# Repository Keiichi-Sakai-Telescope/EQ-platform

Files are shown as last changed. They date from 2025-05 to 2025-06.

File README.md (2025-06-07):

## これは何か？

40cmドブソニアンなどに使っている赤道台(Equatorial Platform)の設計や実験の結果など雑多なものを置いています。タミヤの6速HEというギヤボックスを活用して低消費電力な追尾を目指していました。RE-260互換モーターをそのまま使用し、センサなしで恒星時追尾します。
もともと55cmドブソニアンのポンセットマウントを作ってたので、Poncetという単語が散見されますが、それすらGee式で、最終的な実装のかたちは独自形式です。もし読めそうなファイルがあれば眺めていただければと思います。

このプロジェクトはSubversionで管理していましたが、データシートなど大きなバイナリを含んでいたため、gitに変換すると非常に大きくなったために、主要なファイルのみgithubに上げることにしました。
そういう経緯のためにgit cloneしたところで何かできるものではなく、過去にこんなの作って実験してましたという記録を残すことが目的です。プロジェクトの残骸ですね。。。

## 開発環境

* MPLAB X<br/>新しくても古くても動かないと思います。アセンブラとリンカーがよく変わるので、動くバージョンを探す必要があります。
* XCircuit<br/>Linux環境で使っていた回路図CADです。
* Pcb<br/>Linux環境で使っていたプリント基板CADです。
* QCad もしくは LibreCAD<br/>2D CADです。ファイルはDXF形式ですが、LibreCADでもQCadでも見栄えがよく変わります。標準規格がないんですね。
* GNU bc<br/>任意精度の計算コマンドです。表引き用の数値を計算するのに使ってました。

## MPLab Xのプロジェクトたち

複数試作しましたが、世の中に出回っている基板はPIC16F1825を使った新旧2種類の基板のみです。外見上の区別は3.5mmミニジャックがある(新)かない(古)か、内部ではMOSFETの駆動用にインバータICが入ってる(新)か入ってない(古)かです。

* FB-UB-16F18345.X<br/>PIC16F18345による試作です。これを実装した架台は無いです。
* FB-UB-16F18857.X<br/>PIC16F18857による試作です。これを実装した架台は無いです。
* FB-UB-18F25Q10.X<br/>PIC18F25Q10による試作です。これを実装した架台は無いです。
* FB-USB.X<br/>検討のみ。試作してない。
* FB-minimal.X<br/>検討のみ。試作してない。
* Flasher.X<br/>ストロボスコープを持ち歩くのは大げさなので、PIC16F1825基板を流用してLEDによるストロボスコープもどきを作ってました。
* HB-B-16F1825.X<br/>PIC16F1825による実装です。5.5Vまで動作することを目指しています。3.5mmステレオジャックを実装している新しい基板ではこのソフトウェアを書き込む必要があります。電源電圧の変化には安定ですが、ADCのVrefを2.048V設定とすることによる動作下限電圧があります。
* HB-B-16LF1825.X<br/>PIC16F1825による実装です。MCUの動作下限電圧まで動作することを目指しています。3.5mmステレオジャックを実装している新しい基板ではこのソフトウェアを書き込む必要があります。LF版MCUによる実装を目指していましたが、LF版を使う強い理由がなくてLF版で実装してません。ADCのVrefが電源電圧なので、5V近くなると1LSBの電圧が大きくなって制御が不安定になるかもしれません。
* HB-CC.X<br/>検討のみ。試作してない。
* HB-UB-16F1825.X<br/>PIC16F1825による実装です。5.5Vまで動作することを目指しています。3.5mmステレオジャックを実装していない古い基板ではこのソフトウェアを書き込む必要があります。電源電圧の変化には安定ですが、ADCのVrefを2.048V設定とすることによる動作下限電圧があります。
* HB-UB-16LF1825.X<br/>PIC16F1825による実装です。MCUの動作下限電圧まで動作することを目指しています。3.5mmステレオジャックを実装していない古い基板ではこのソフトウェアを書き込む必要があります。LF版MCUによる実装を目指していましたが、LF版を使う強い理由がなくてLF版で実装してません。ADCのVrefが電源電圧なので、5V近くなると1LSBの電圧が大きくなって制御が不安定になるかもしれません。
* HB-VC.X<br/>検討のみ。試作してない。

乾電池やニッケル水素充電池を3本使用し、新しい基板ならHB-B-16F1825.Xからのソフトウェアを書き込むとよいはずです。
SP赤道儀など軽負荷の場合は電池2本でも動きますが、2本の場合はHB-B-16LF1825.Xを使う必要があります。

## 外部信号

* 巻き戻しSW<br/>
追尾開始位置を知らせるスイッチを接続します。必須です。
* 動作限界SW<br/>
単方向噛合ナット(改造したウルトラナッターなど)を使ってない場合、動作限界を超えたら止めるように指示するスイッチを接続します。単方向噛合ナットを使っている場合は空回りするだけなので不要です。
* 停止SW<br/>
半自動追尾のときの停止スイッチを接続します。新しい基板では3.5mmミニジャックを接続端子として実装しています。
* 2倍速SW<br/>
半自動追尾のときの2倍速スイッチを接続します。新しい基板では3.5mmミニジャックを接続端子として実装しています。

## ギヤボックスやモーターなど

タミヤの6速HEとそれに付属するRE-260モーターに合わせてありますが、モーター定数定義を替えることにより他のマブチ互換の模型用モーターでも動きます。
なお、モーターの回転数が定格の1/10くらいのところで一定速度の制御をかけるように設計されており、motor.incにモーター定数が定義されています。
そして、たとえば6-speed-4th-40min-16in.sが現在使用中の40cmドブソニアンの追尾架台に組み込んでいる速度表です。この速度票を巻き戻したときに頭から読み、最後に達したら止まります。
また、有限の速度表を使わず、表を無限に循環して使用する設定もでき、SP赤道儀向けなどではそうしています。いずれにせよ、motor.incに記述があるので読んでください。

本実装ではタミヤの6速HE推しですが、これは安いし入手性がいいし6速から選べるし1300分の1まで減速できるし平歯車だけで構成されてていずれも高効率なため、SP赤道儀といった軽負荷用途にもアンバランスな追尾架台といった重負荷用途にも最適であると考えています。
実際に、SP赤道儀のような軽負荷では消費電流20mA前後、40㎝ドブソニアンのような重負荷用途では消費電流100mA前後となります。エネループ単三でそれぞれ100時間と20時間相当です。

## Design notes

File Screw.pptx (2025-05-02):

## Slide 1

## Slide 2

トルク
ピッチ
有効径
リード角
摩擦係数
摩擦角
頂角÷２

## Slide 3

トルク[kgf-cm]
ピッチ = 1.75mm
有効径 = 10.863mm
リード角 = 2.938° = 0.0513 rad
摩擦係数 = 0.3
摩擦角 = 19.848° = 0.3464 rad
頂角÷２ = 30° = π/6 rad

M12P1.75, μ=0.3 で持ち上げる場合

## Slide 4

トルク[kgf-cm]
ピッチ = 1.75mm
有効径 = 10.863mm
リード角 = 2.938° = 0.0513 rad
摩擦係数 = 0.3
摩擦角 = 19.848° = 0.3464 rad
頂角÷２ = 30° = π/6 rad

M12P1.75, μ=0.3 で繰り下げる場合

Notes: p=1.75
d=10.863
m=0.3
20/d/t(a(m/c(3.14159/6))-a(p/d/3.14159))

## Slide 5

トルク[kgf-cm]
ピッチ = 25.4/16 mm = 1.5875mm
有効径 = 8.509mm
リード角
摩擦係数 = 0.3
摩擦角
頂角÷２ = 27.5° = 55π/360 rad

W3/8 16T/in, μ=0.3 で持ち上げる場合
繰り下げる場合は8.60T

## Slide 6

トルク[kgf-cm]
ピッチ = 49/17 mm = 2.88mm
有効径 = 4mm
リード角=0.225[rad]
摩擦係数 = 0.3
摩擦角
頂角÷２ = 27.5° = 55π/360 rad

細軸コース, μ=0.3 で持ち上げる場合
繰り下げる場合は44T

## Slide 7

正三角形

z

y

60°

x

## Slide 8

南天赤道儀？

z

y

φ

x

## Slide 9

z

y

90°

x

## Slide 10

y

天板

90-緯度

0

x

x軸が蝶番の軸

底板

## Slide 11

t, δは分の単位とすると
motor_speedはrpmの単位となる。
そのとき、ω=2π/1436.0681755 である。
同様にt, δが秒の単位では、
motor_speedはrpsの単位で、
ω=2π/86164.09053 である。

y

＋　　　　　　ー

y

0

90-緯度

x

z

x軸が蝶番の軸

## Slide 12

固定点と可動点を任意に置く場合

可動点

図のような位置に固定点を置くと、
固定点の角度変化が少なくなる。
ナットを固定点側に置くのも良いかも。
固定と可動は図を書く都合なので、
入れ替えて考えることは可能。

固定点

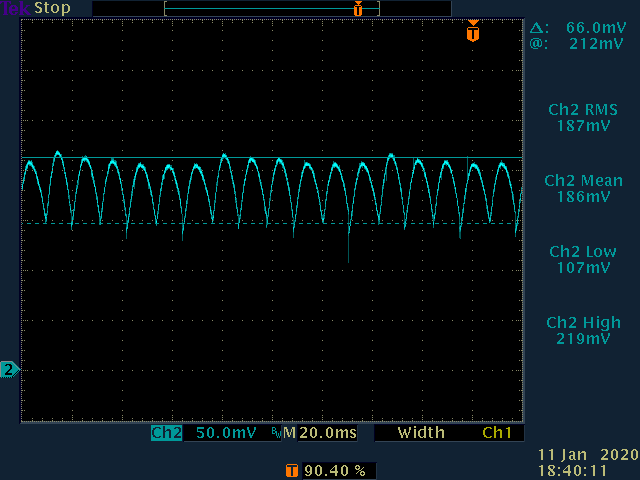
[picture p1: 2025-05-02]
900rpm_RE-260_new_mabuchi.TIF

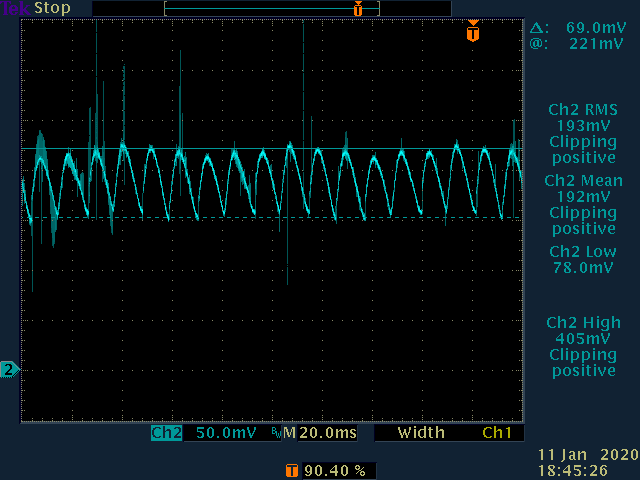
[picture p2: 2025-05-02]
900rpm_RE-260_asahi.TIF

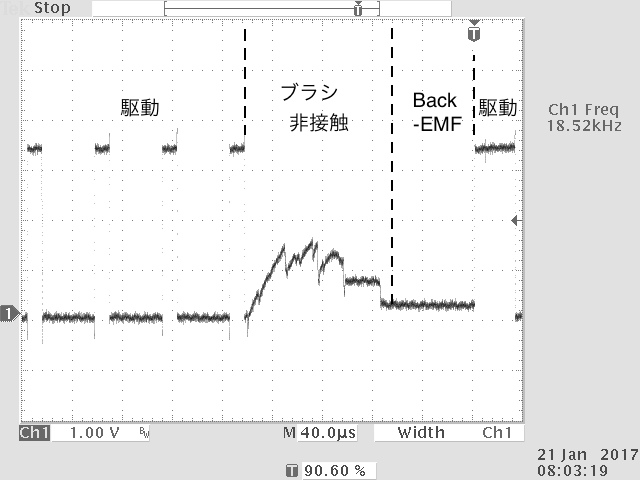
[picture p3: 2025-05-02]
inv-TEK00004.png

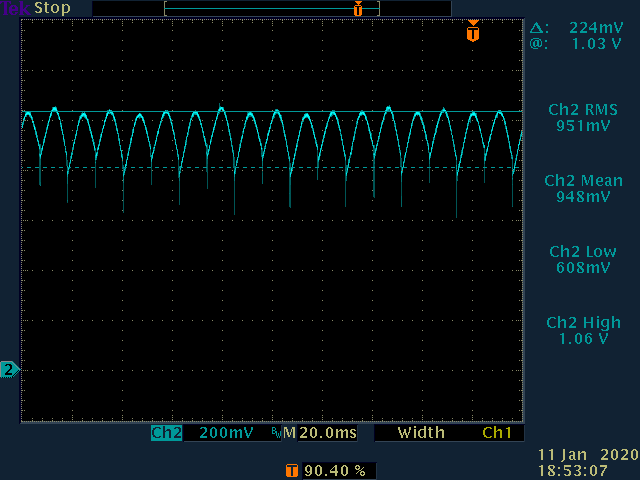
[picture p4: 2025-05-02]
900rpm_RF-500_mabuchi.TIF

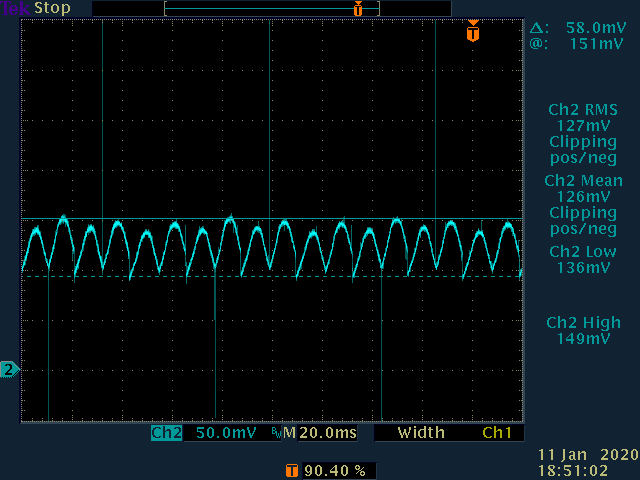
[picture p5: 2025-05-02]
900rpm_FA-130_new_mabuchi.TIF

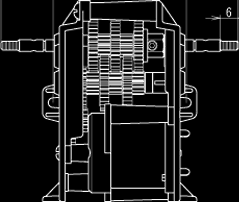
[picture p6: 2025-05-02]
72005-top.png

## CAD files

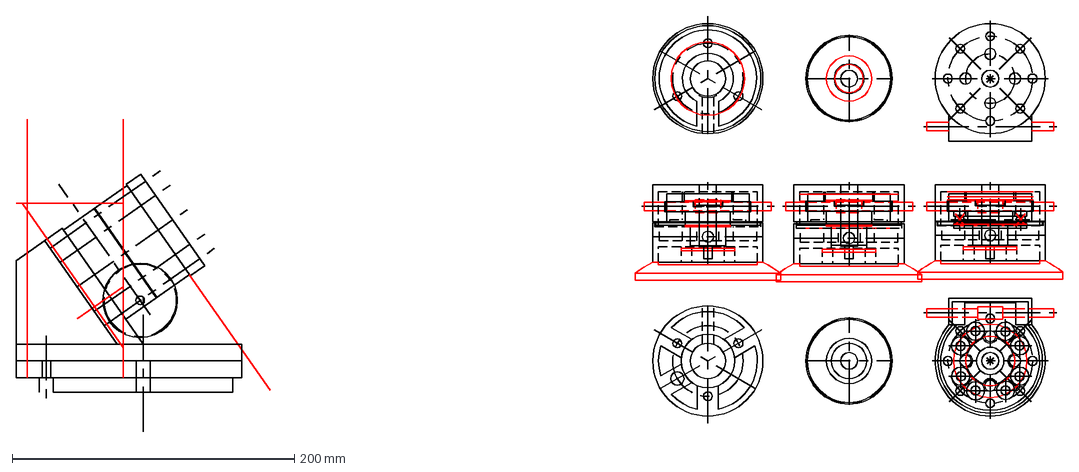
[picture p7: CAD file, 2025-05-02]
Porta.dxf
741.5 x 294.0 mm

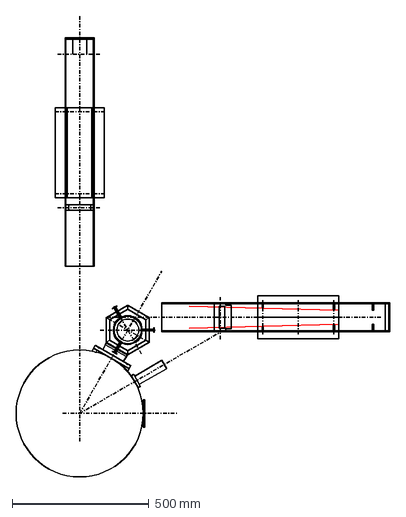
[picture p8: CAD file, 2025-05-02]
8cm-Mount.dxf
1365.0 x 1683.3 mm

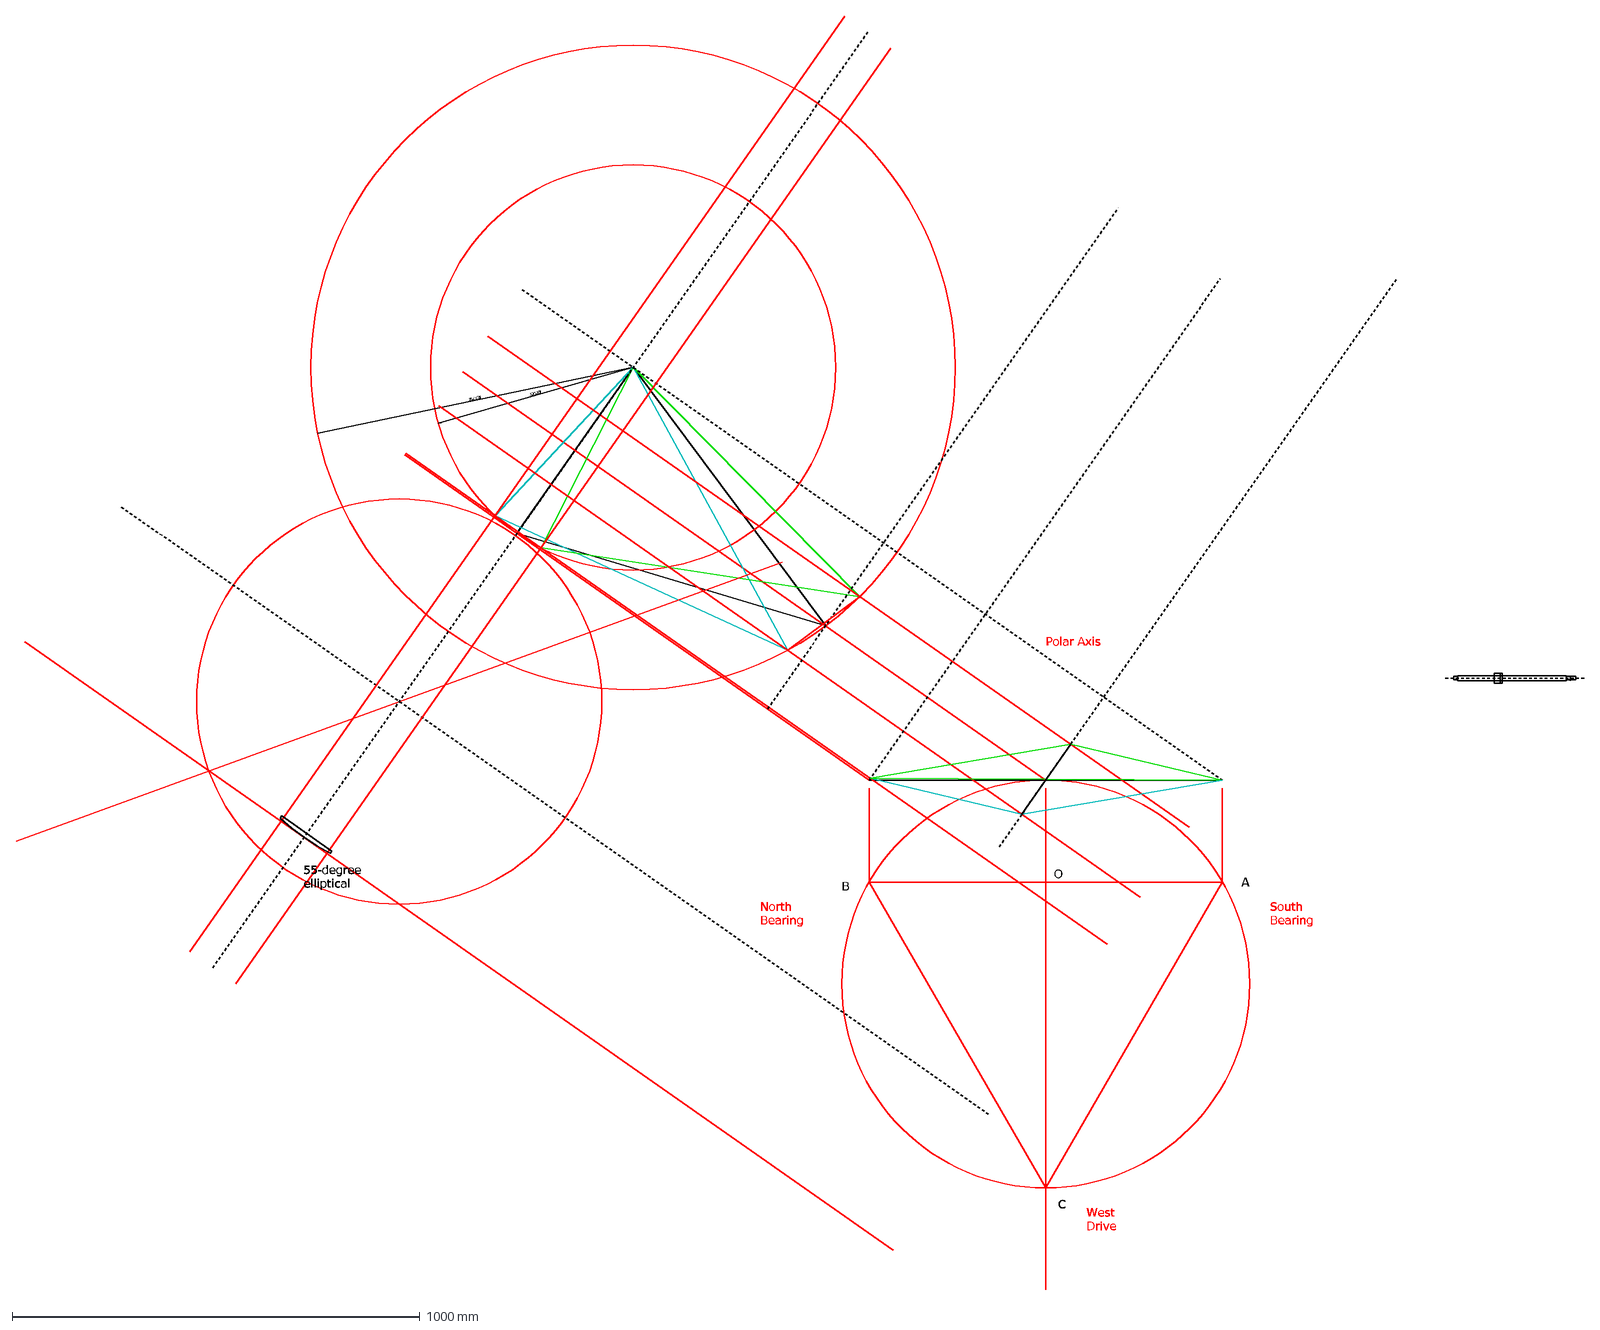
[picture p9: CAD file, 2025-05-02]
Unbalanced-EQ-8cm-Type1.dxf
496,73
790,05
A
B
C
O
South Bearing
North Bearing
West Drive
Polar Axis
55-degree elliptical

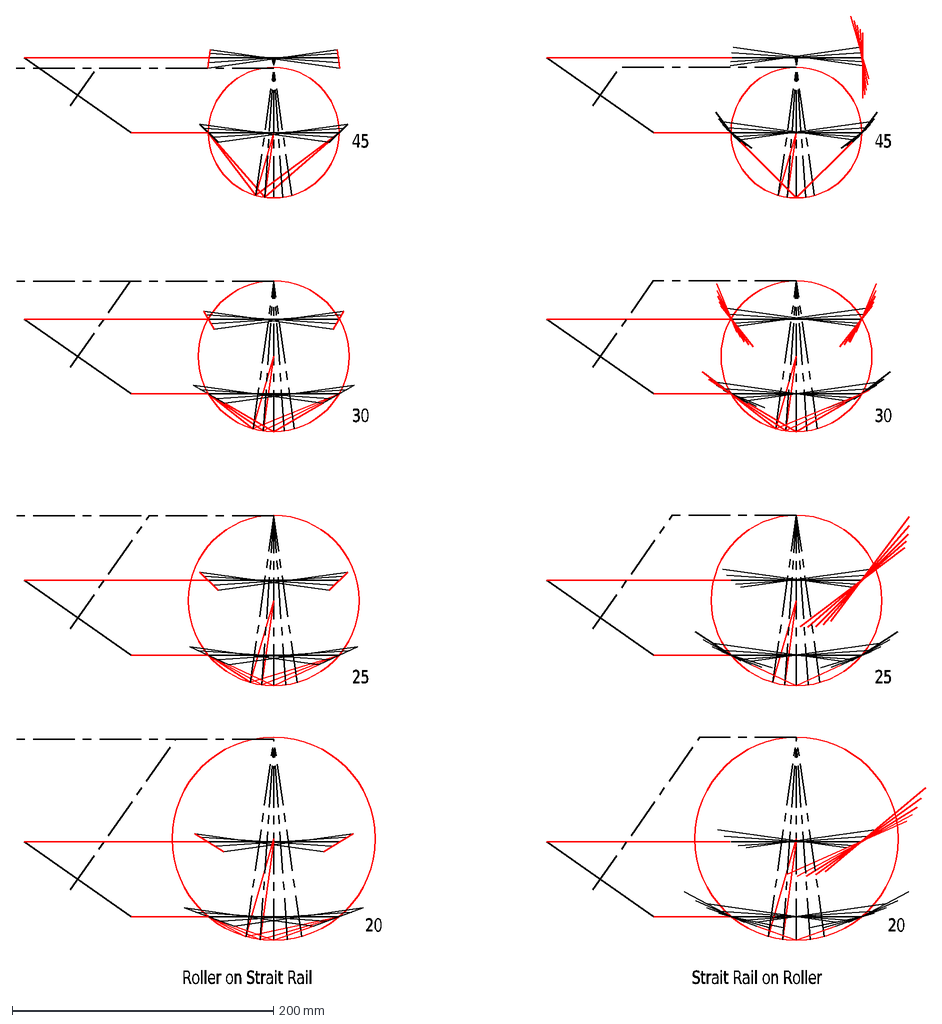
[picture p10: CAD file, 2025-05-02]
circumferential.dxf
Roller\~on\~Strait\~Rail
20
25
30
45
Strait\~Rail\~on\~Roller

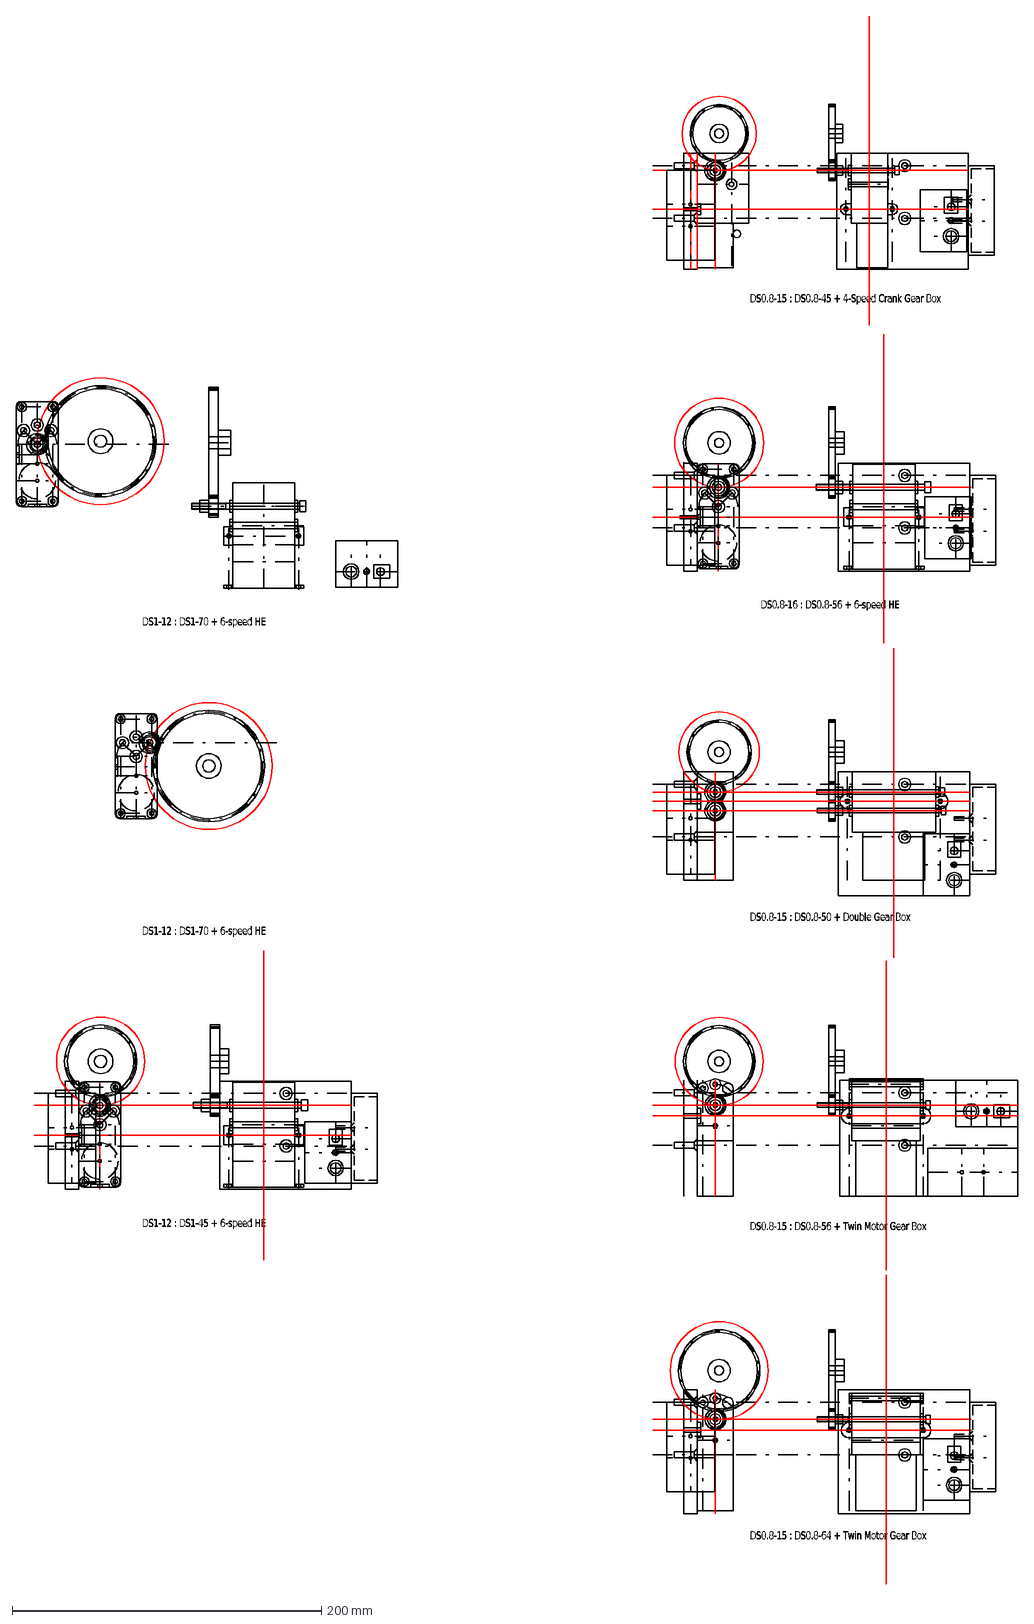
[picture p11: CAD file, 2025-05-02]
6-Speed_HE.dxf
DS1-12\~:\~DS1-70\~+\~6-speed\~HE
DS1-12\~:\~DS1-45\~+\~6-speed\~HE
DS0.8-16\~:\~DS0.8-56\~+\~6-speed\~HE
DS0.8-15\~:\~DS0.8-50\~+\~Double\~Gear\~Box
DS0.8-15\~:\~DS0.8-45\~+\~4-Speed\~Crank\~Gear\~Box
DS0.8-15\~:\~DS0.8-56\~+\~Twin\~Motor\~Gear\~Box
DS0.8-15\~:\~DS0.8-64\~+\~Twin\~Motor\~Gear\~Box

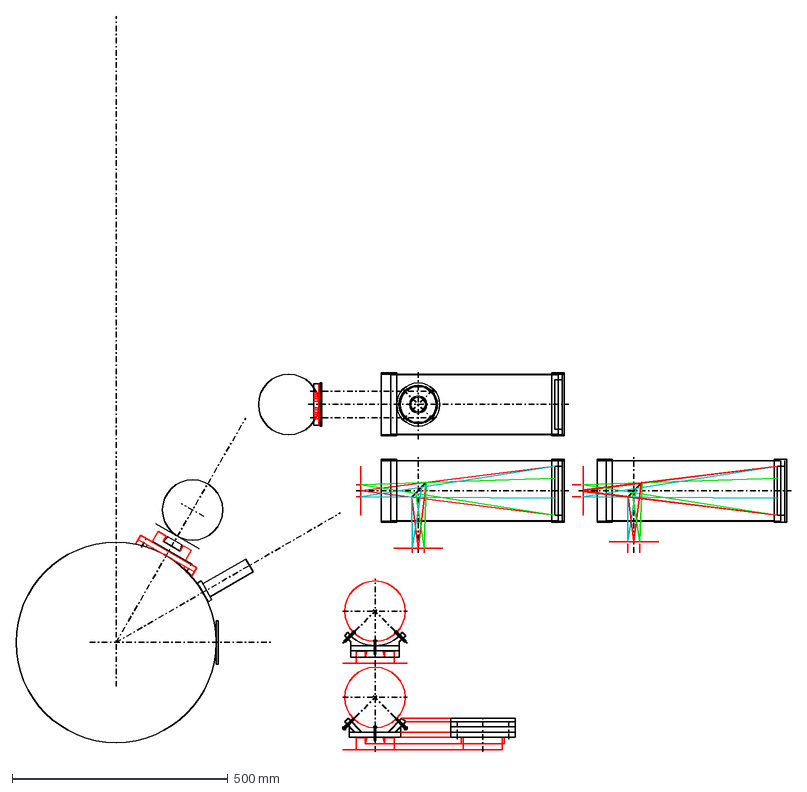
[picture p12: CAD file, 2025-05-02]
SE-AT100n-Mount.dxf
1796.0 x 1705.0 mm

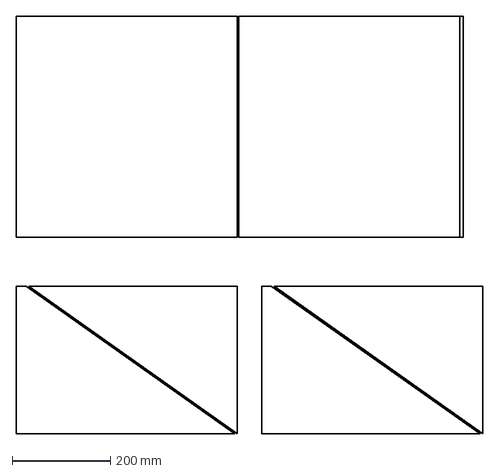
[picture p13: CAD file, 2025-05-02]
cutting-plan.dxf
950.0 x 850.0 mm

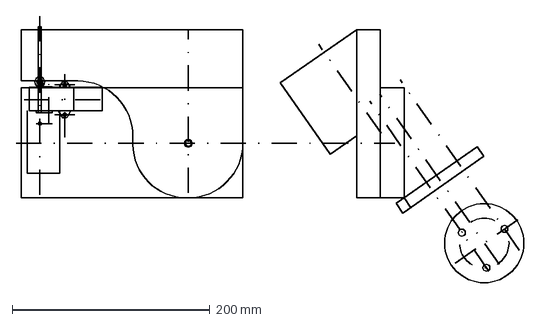
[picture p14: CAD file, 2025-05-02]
Kolkit.dxf
512.9 x 269.1 mm

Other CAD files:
Poncet450.dxf
16in-Tube.dxf
Unbalanced-EQ-8cm-Type2.dxf
SuperPolaris.dxf
GearBox.dxf
16in-Mount.dxf
Poncet480-mirrored-hinge.dxf
Gee-8cm.dxf
Poncet480.dxf
Poncet480-mirrored.dxf

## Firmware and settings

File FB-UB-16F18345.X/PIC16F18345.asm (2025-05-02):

						#include		mpasmx.inc

						errorlevel -302
						radix	DEC

FCY						equ		4000000	; 4MHz, instruction cycle
PWM_PERIOD				equ		200		; PWM frequency = FCY/PWM_PERIOD, min: 200, max: 256
OPEN_LOOP_PERIOD		equ		62500					; fixed settings
ADC_INTERVAL			equ		15

 __config	_CONFIG1,	_FEXTOSC_HS & _RSTOSC_HFINT1
 __config	_CONFIG2,	_MCLRE_OFF & _PPS1WAY_OFF & _WDTE_ON & _BOREN_SLEEP & _BORV_LOW & _LPBOREN_OFF
 __config	_CONFIG3,	_LVP_OFF

LOW_BATT_ERROR			set		2700	; [mV]
LOW_BATT_WARNING		set		3000	; [mV]

POLLING_FREQUENCY		equ		4

SIDEREAL_TIME_0p16		equ		65536		; [0.5, 1.5)
SOLAR_TIME_0p16			equ		65715		; [0.5, 1.5)
LUNAR_TIME_0p16			equ		68019		; [0.5, 1.5)

DECIDE_PRESCALER		macro	MOTOR_100TH_RPM
						local	sampling_rpm, threshold_8th

sampling_rpm = (MOTOR_100TH_RPM)*2	; double sampling / wave
		if (MODE_NORMAL_SPEED == SAMPLING_SINGLE) || (MODE_NORMAL_SPEED == SAMPLING_MOVING_AVERAGE) || (MODE_DOUBLE_SPEED == SAMPLING_HALF)
sampling_rpm = (MOTOR_100TH_RPM)	; single sampling / wave
		endif
		if (MODE_NORMAL_SPEED == SAMPLING_HALF)
sampling_rpm = (MOTOR_100TH_RPM)/2	; half sampling / wave
		endif

; calculate threshold by the slowest speed
; FCY*1000/65536 * LUNAR_TIME_0p16/65536 / 4 + 1
threshold_8th = ( ( (FCY*(1000/4)) / 65536) * (LUNAR_TIME_0p16) ) / 65536 + 1

		if ((sampling_rpm) <= threshold_8th)
T1_PRESCALER			equ		3	; 1:8
		else
			if ((sampling_rpm) <= (threshold_8th*2))
T1_PRESCALER			equ		2	; 1:4
			else
				if ((sampling_rpm) <= (threshold_8th*4))
T1_PRESCALER			equ		1	; 1:2
				else
T1_PRESCALER			equ		0	; 1:1
				endif
			endif
		endif
	endm
#define	FCY_SCALED	(FCY >> T1_PRESCALER)

; sampling period[clock] = FCY_SCALED[clock/s]*10/MOTOR_RPM
LUT_ENTRIES				macro	MOTOR_100TH_RPM
						local	dividend, divisor, period_i, period_f, fraction

dividend = FCY_SCALED*(1000 >> 3)
	if (MODE_NORMAL_SPEED == SAMPLING_SINGLE) || (MODE_NORMAL_SPEED == SAMPLING_MOVING_AVERAGE)
divisor  = (MOTOR_100TH_RPM)	; normal sampling
	endif
	if (MODE_NORMAL_SPEED == SAMPLING_DOUBLE)
divisor  = (MOTOR_100TH_RPM)*2	; double sampling
	endif
	if (MODE_NORMAL_SPEED == SAMPLING_HALF)
divisor  = (MOTOR_100TH_RPM)/2	; half sampling
	endif
period_i = dividend/divisor
period_f = ((dividend - period_i*divisor) << 3)*32/divisor
period_i = (period_i << 3) + (period_f >> 5)
period_f = period_f & 0x1F

fraction = period_f
		dw		0x3F00 | (LOW period_i)
		dw		0x3F00 | (HIGH period_i)
		while fraction != 0
fraction += period_f
				if fraction >= 32
fraction -= 32
						dw		0x3F00 | (LOW (period_i + 1))
						dw		0x3F00 | (HIGH (period_i + 1))
				else
						dw		0x3F00 | (LOW period_i)
						dw		0x3F00 | (HIGH period_i)
				endif
		endw
						endm

LUT_ENTRY				macro	MOTOR_10TH_RPM
						local	period_i

	if (MODE_NORMAL_SPEED == SAMPLING_SINGLE) || (MODE_NORMAL_SPEED == SAMPLING_MOVING_AVERAGE)
period_i = (FCY_SCALED*100 + (MOTOR_10TH_RPM)/2)/(MOTOR_10TH_RPM)	; normal sampling
	endif
	if (MODE_NORMAL_SPEED == SAMPLING_DOUBLE)
period_i = (FCY_SCALED*50 + (MOTOR_10TH_RPM)/2)/(MOTOR_10TH_RPM)	; double sampling
	endif
	if (MODE_NORMAL_SPEED == SAMPLING_HALF)
period_i = (FCY_SCALED*200 + (MOTOR_10TH_RPM)/2)/(MOTOR_10TH_RPM)	; half sampling
	endif

						dw		0x3F00 | (LOW period_i)
						dw		0x3F00 | (HIGH period_i)
						endm

_CYCLE_TIME_L			equ		0						; cycle time is [T1CK] in 16p0
_CYCLE_TIME_H			equ		1
_SIZEOF_LUT_ENTRY		equ		2						; fixed. don't change

; gain
;P_GAIN					proportional gain(amplitude)
;I_TIME_8p8				integration time(amplitude) where the range is from 2.0 to 256.0
; proportional_error = P_GAIN*(target_voltage - cemf_voltage)
; duty_ratio = (proportional_error + integral_error) / supplied_voltage
;	integral_error += proportional_error/I_TIME_8p8

; sampling mode
;MODE_NORMAL_SPEED		sampling mode at normal speed
;MODE_DOUBLE_SPEED		sampling mode at double speed
;	sampling modes are following.
SAMPLING_SINGLE			equ		0		; single sampling
SAMPLING_MOVING_AVERAGE	equ		1		; single sampling and averaging with previous sample
SAMPLING_DOUBLE			equ		2		; double sampling with phase control
SAMPLING_HALF			equ		3		; half sampling

lut						code
pfm_lut_start:
						#include ../motor.inc
pfm_lut_end:
OPEN_LOOP_FREQ			equ		(FCY_SCALED/OPEN_LOOP_PERIOD)
						LUT_ENTRY	OPEN_LOOP_FREQ*100

; Vin*duty = Rcoil*Is + target_voltage
; duty = (Rcoil*Is + target_voltage)/Vin
STARTUP_VOLTAGE_15p1	equ		MOTOR_RESISTANCE*STARTUP_CURRENT*3/2*2/1000	; IR-drop, 2LSB=1mV	[V]

; target_voltage[LSB] = FCY_SCALED/period*10 / MOTOR_SPEED_CONSTANT * 500[LSB/V]
;                     = FCY_SCALED*5000/MOTOR_SPEED_CONSTANT / period
; FCY_SCALED*5000/MOTOR_SPEED_CONSTANT = period*target_voltage

MEAN_MOTOR_SPEED_CONSTANT   = (MOTOR_SPEED_CONSTANT*PEAK_WAVE_HEIGHT + CENTER_WAVE_HEIGHT/2)/CENTER_WAVE_HEIGHT
; MOTOR_CONSTANT_init = FCY_SCALED*10*500[LSB/V]/MEAN_MOTOR_SPEED_CONSTANT
MOTOR_CONSTANT_init = (FCY_SCALED*10)                                                /MEAN_MOTOR_SPEED_CONSTANT
MOTOR_CONSTANT_init = (FCY_SCALED*10 - MOTOR_CONSTANT_init*MEAN_MOTOR_SPEED_CONSTANT)*500/MEAN_MOTOR_SPEED_CONSTANT + MOTOR_CONSTANT_init*500

						; Test
CLKRCON_init			equ		(1<<CLKREN)|(B'10'<<CLKRDC0)|(B'000'<<CLKRDIV0)	; Fcy
CLC1CON_init			equ		(1<<LC1EN)|(B'010'<<LC1MODE0)	; 4-input AND
CLC1POL_init			equ		B'1110'
						#include test.inc

	if (MODE_NORMAL_SPEED == SAMPLING_SINGLE)
MULT_PERIOD_1X_24p8		equ		256		; 1.0
CALC_SAMPLES_1X			equ		0		; no calculation
	endif
	if (MODE_NORMAL_SPEED == SAMPLING_MOVING_AVERAGE)
MULT_PERIOD_1X_24p8		equ		256		; 1.0
CALC_SAMPLES_1X			equ		1		; averaging
	endif
	if (MODE_NORMAL_SPEED == SAMPLING_DOUBLE)
MULT_PERIOD_1X_24p8		equ		128		; 0.5
CALC_SAMPLES_1X			equ		2		; phase control
	endif
	if (MODE_NORMAL_SPEED == SAMPLING_HALF)
MULT_PERIOD_1X_24p8		equ		512		; 2.0
CALC_SAMPLES_1X			equ		0		; no calculation
	endif
MULT_VOLTAGE_1X_24p8	equ		MULT_PERIOD_1X_24p8
MULT_ITIME_1X_24p8		equ		65536/MULT_PERIOD_1X_24p8

	if (MODE_DOUBLE_SPEED == SAMPLING_SINGLE)
MULT_PERIOD_2X_24p8		equ		256/2	; 0.5
CALC_SAMPLES_2X			equ		0		; no calculation
	endif
	if (MODE_DOUBLE_SPEED == SAMPLING_MOVING_AVERAGE)
MULT_PERIOD_2X_24p8		equ		256/2	; 0.5
CALC_SAMPLES_2X			equ		1		; averaging
	endif
	if (MODE_DOUBLE_SPEED == SAMPLING_DOUBLE)
MULT_PERIOD_2X_24p8		equ		128/2	; 0.25
CALC_SAMPLES_2X			equ		2		; phase control
	endif
	if (MODE_DOUBLE_SPEED == SAMPLING_HALF)
MULT_PERIOD_2X_24p8		equ		512/2	; 1.0
CALC_SAMPLES_2X			equ		0		; no calculation
	endif
MULT_VOLTAGE_2X_24p8	equ		2*MULT_PERIOD_2X_24p8
MULT_ITIME_2X_24p8		equ		65536/MULT_PERIOD_2X_24p8
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

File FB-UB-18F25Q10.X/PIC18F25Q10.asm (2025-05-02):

						#include		mpasmx.inc

						errorlevel -302
						radix	DEC

FCY						equ		6000000					; 6MHz
PWM_PERIOD				equ		250						; PWM frequency = FCY/PWM_PERIOD, min: 200, max: 256
OPEN_LOOP_PERIOD		equ		62500					; fixed settings
ADC_INTERVAL			equ		15

;	boot
;	por/mclr			other reset
;	HP Regulator		LP Regulator
;	HFINTOSC			wait for wakeup
;	EXTOSC				reset

; High supply voltage or Low motor speed
						CONFIG	FEXTOSC = HS         ; HS (crystal oscillator) above 8 MHz; PFM set to high power
						CONFIG	RSTOSC = HFINTOSC_1MHZ	; HFINTOSC with HFFRQ = 4 MHz and CDIV = 4:1
						CONFIG	CLKOUTEN = OFF       ; CLKOUT function is disabled
						CONFIG	CSWEN = ON           ; Writing to NOSC and NDIV is allowed
						CONFIG	FCMEN = ON           ; Fail-Safe Clock Monitor enabled
						CONFIG	MCLRE = INTMCLR      ; MCLR pin (RE3) is input
						CONFIG	PWRTE = OFF          ; Power up timer disabled
						CONFIG	LPBOREN = OFF        ; Low power BOR is disabled
						CONFIG	BOREN = NOSLP        ; Brown-out Reset enabled while running, disabled in Sleep; SBOREN is ignored
						CONFIG	BORV = VBOR_190      ; Brown-out Reset Voltage (VBOR) set to 1.90V
						CONFIG	ZCD = OFF            ; ZCD disabled. ZCD can be enabled by setting the ZCDSEN bit of ZCDCON
						CONFIG	PPS1WAY = OFF        ; PPSLOCK bit can be set and cleared repeatedly (subject to the unlock sequence)
						CONFIG	STVREN = ON          ; Stack full/underflow will cause Reset
						CONFIG	XINST = OFF          ; Extended Instruction Set and Indexed Addressing Mode disabled
						CONFIG	WDTCPS = WDTCPS_31   ; Divider ratio 1:65536; software control of WDTPS
						CONFIG	WDTE = ON            ; WDT always enabled
						CONFIG	WDTCWS = WDTCWS_7    ; window always open (100%); software control; keyed access not required
						CONFIG	WDTCCS = LFINTOSC    ; WDT reference clock is the 31.0 kHz LFINTOSC
						CONFIG	WRT0 = OFF           ; Block 0 (000800-001FFFh) not write-protected
						CONFIG	WRT1 = OFF           ; Block 1 (002000-003FFFh) not write-protected
						CONFIG	WRTC = OFF           ; Configuration registers (300000-30000Bh) not write-protected
						CONFIG	WRTB = OFF           ; Boot Block (000000-0007FFh) not write-protected
						CONFIG	WRTD = OFF           ; Data EEPROM not write-protected
						CONFIG	SCANE = OFF          ; Scanner module is NOT available for use, SCANMD bit is ignored
						CONFIG	LVP = OFF            ; HV on MCLR/VPP must be used for programming
						CONFIG	CP = ON              ; UserNVM code protection enabled
						CONFIG	CPD = ON             ; DataNVM code protection enabled
						CONFIG	EBTR0 = OFF          ; Block 0 (000800-001FFFh) not protected from table reads executed in other blocks
						CONFIG	EBTR1 = OFF          ; Block 1 (002000-003FFFh) not protected from table reads executed in other blocks
        ifdef __18F25Q10
						CONFIG	EBTR2 = OFF          ; Block 2 (004000-005FFFh) not protected from table reads executed in other blocks
						CONFIG	EBTR3 = OFF          ; Block 3 (006000-007FFFh) not protected from table reads executed in other blocks
		endif
						CONFIG	EBTRB = OFF          ; Boot Block (000000-0007FFh) not protected from table reads executed in other blocks

LOW_BATT_ERROR			set		2000	; [mV]
LOW_BATT_WARNING		set		2200	; [mV]

POLLING_FREQUENCY		equ		4

SIDEREAL_TIME_0p16		equ		65536		; [0.5, 1.5)
SOLAR_TIME_0p16			equ		65715		; [0.5, 1.5)
LUNAR_TIME_0p16			equ		68019		; [0.5, 1.5)

DECIDE_PRESCALER		macro	MOTOR_100TH_RPM
						local	sampling_rpm, threshold_8th

sampling_rpm = (MOTOR_100TH_RPM)*2	; double sampling / wave
		if (MODE_NORMAL_SPEED == SAMPLING_SINGLE) || (MODE_NORMAL_SPEED == SAMPLING_MOVING_AVERAGE) || (MODE_DOUBLE_SPEED == SAMPLING_HALF)
sampling_rpm = (MOTOR_100TH_RPM)	; single sampling / wave
		endif
		if (MODE_NORMAL_SPEED == SAMPLING_HALF)
sampling_rpm = (MOTOR_100TH_RPM)/2	; half sampling / wave
		endif

; calculate threshold by the slowest speed
; FCY*1000/65536 * LUNAR_TIME_0p16/65536 / 4 + 1
threshold_8th = ( ( (FCY*(1000/4)) / 65536) * (LUNAR_TIME_0p16) ) / 65536 + 1

		if ((sampling_rpm) <= threshold_8th)
T1_PRESCALER			equ		3	; 1:8
		else
			if ((sampling_rpm) <= (threshold_8th*2))
T1_PRESCALER			equ		2	; 1:4
			else
				if ((sampling_rpm) <= (threshold_8th*4))
T1_PRESCALER			equ		1	; 1:2
				else
T1_PRESCALER			equ		0	; 1:1
				endif
			endif
		endif
	endm
#define	FCY_SCALED	(FCY >> T1_PRESCALER)

; sampling period[clock] = FCY_SCALED[clock/s]*10/MOTOR_RPM
LUT_ENTRIES				macro	MOTOR_100TH_RPM
						local	dividend, divisor, period_i, period_f, fraction

dividend = FCY_SCALED*(1000 >> 3)
	if (MODE_NORMAL_SPEED == SAMPLING_SINGLE) || (MODE_NORMAL_SPEED == SAMPLING_MOVING_AVERAGE)
divisor  = (MOTOR_100TH_RPM)	; normal sampling
	endif
	if (MODE_NORMAL_SPEED == SAMPLING_DOUBLE)
divisor  = (MOTOR_100TH_RPM)*2	; double sampling
	endif
	if (MODE_NORMAL_SPEED == SAMPLING_HALF)
divisor  = (MOTOR_100TH_RPM)/2	; half sampling
	endif
period_i = dividend/divisor
period_f = ((dividend - period_i*divisor) << 3)*32/divisor
period_i = (period_i << 3) + (period_f >> 5)
period_f = period_f & 0x1F

fraction = period_f
		dw		period_i
		while fraction != 0
fraction += period_f
				if fraction >= 32
fraction -= 32
						dw		(period_i + 1)
				else
						dw		period_i
				endif
		endw
						endm

LUT_ENTRY				macro	MOTOR_10TH_RPM
						local	period_i

	if (MODE_NORMAL_SPEED == SAMPLING_SINGLE) || (MODE_NORMAL_SPEED == SAMPLING_MOVING_AVERAGE)
period_i = (FCY_SCALED*100 + (MOTOR_10TH_RPM)/2)/(MOTOR_10TH_RPM)	; normal sampling
	endif
	if (MODE_NORMAL_SPEED == SAMPLING_DOUBLE)
period_i = (FCY_SCALED*50 + (MOTOR_10TH_RPM)/2)/(MOTOR_10TH_RPM)	; double sampling
	endif
	if (MODE_NORMAL_SPEED == SAMPLING_HALF)
period_i = (FCY_SCALED*200 + (MOTOR_10TH_RPM)/2)/(MOTOR_10TH_RPM)	; half sampling
	endif

						dw		period_i
						endm

_CYCLE_TIME_L			equ		0						; cycle time is [T1CK] in 16p0
_CYCLE_TIME_H			equ		1
_SIZEOF_LUT_ENTRY		equ		2						; fixed. don't change

; gain
;P_GAIN					proportional gain(amplitude)
;I_TIME_8p8				integration time(amplitude) where the range is from 2.0 to 256.0
; proportional_error = P_GAIN*(target_voltage - cemf_voltage)
; duty_ratio = (proportional_error + integral_error) / supplied_voltage
;	integral_error += proportional_error/I_TIME_8p8

; sampling mode
;MODE_NORMAL_SPEED		sampling mode at normal speed
;MODE_DOUBLE_SPEED		sampling mode at double speed
;	sampling modes are following.
SAMPLING_SINGLE			equ		0		; single sampling
SAMPLING_MOVING_AVERAGE	equ		1		; single sampling and averaging with previous sample
SAMPLING_DOUBLE			equ		2		; double sampling with phase control
SAMPLING_HALF			equ		3		; half sampling

lut						code
pfm_lut_start:
						#include ../motor.inc
pfm_lut_end:
OPEN_LOOP_FREQ			equ		(FCY_SCALED/OPEN_LOOP_PERIOD)
						LUT_ENTRY	OPEN_LOOP_FREQ*100
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
